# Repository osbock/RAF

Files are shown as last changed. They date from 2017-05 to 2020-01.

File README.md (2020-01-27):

# RAF - Ready...Aim...Fire!
Software for a beginning programming class with Arduino, and IOT programming with MQTT. Hardware consists of an Arduino, Shield, Pan/tilt mechanism and pneumatic components for firing foam darts
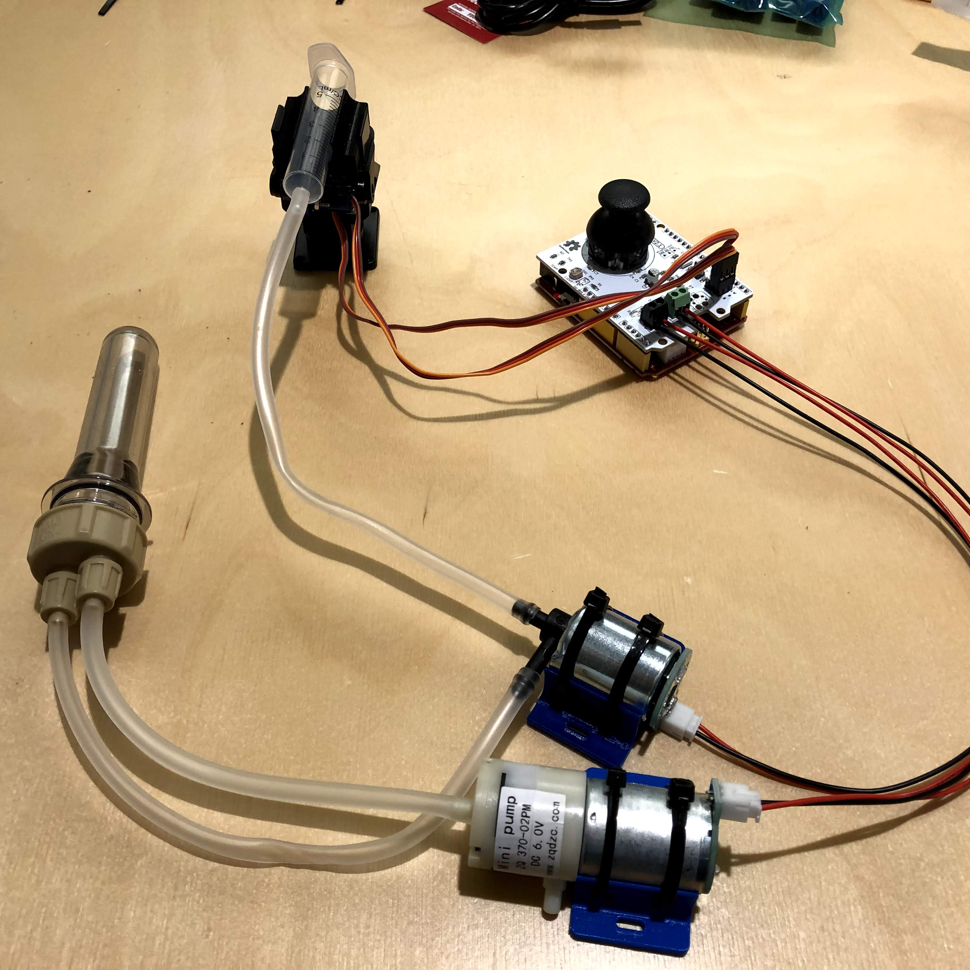
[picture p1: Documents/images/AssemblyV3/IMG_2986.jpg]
overviewpic Overview picture

## Instructions
 * [Assembly Instructions](./Documents/Assembly.md)
 * [Software setup](./Documents/Software.md)

## Software requirements
 * Arduino IDE
 * Python 3.X
 * Adafruit IOT python package

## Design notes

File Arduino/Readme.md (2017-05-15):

# Example Arduino code

 * RAFTest: basic functional test. Serial prints Light and temp sensor, joystick controls servos 3 and 5, button triggers solenoid. LED lights in sequence at boot.

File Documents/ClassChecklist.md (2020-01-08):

# Materials needed for class:
## Instructor Materials
* Assembled Demo Unit
* Extra Arduino and shield for intro to Arduino Part
* USB cable for programming (Instructor)
## Participant materials
* RAF kits (+5-7% for extra parts for failures, or extra parts)
* extra silicone tubing (ammend BOM for next order)
* zip ties (4/kit) (ammend BOM for next order) extra for hose clamp
* usb C -> usb connectors
* foam poster tape for sticking down arduino
* Power squids/extension cords
* Instruction printouts
* 8x10 foam core (1 per participant)
## tools
* 2mm flat head Screw drivers (1 per 4 participants)
* scissors
* flush cutters (optional) for cutting zip ties (can use scissors)
* wire strippers (optional for re-stripping pump and solenoid pigtails)

## Frequent failure parts
* Power Supplies
* Arduinos
* Pan tilts
* Shields
* USB cables (rare)

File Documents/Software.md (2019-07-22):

# Software Setup
 ## Arduino
  * [Arduino](https://www.arduino.cc/en/Main/Software#download)
 
   Note: download and install the desktop version. The WebIDE is untested with these course materials.
   
 ## Sample code/Arduino Libraries
 Clone or [download the zip](https://github.com/osbock/RAF/archive/master.zip) of this repository

 ## Optional setup for IOT activities
 Note: these instructions are dated and probably require updates for Python 3.x
 ## Adafruit.io
   * Get an account at [Adafruit.com](https://adafruit.com)
   * Sign up for [Adafruit.io](https://io.adafruit.com/)
   
 * [Python 2.7](https://www.python.org/downloads/release/python-2713/) (note: preinstalled on most macs)
 * Pip -- comes installed with the python.org download
 * PySerial -- pip install pyserial (sudo pip install pyserial #mac and linux)
 * [Adafruit IO](https://github.com/adafruit/io-client-python)
   * If you have pip installed, sudo pip install adafruit-io
   * otherwise, unzip repository, and python setup.py install

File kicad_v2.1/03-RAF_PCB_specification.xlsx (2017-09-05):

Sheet: Template
PCB Name 名称 | RAF Shield
Board Size 尺寸 | Length*width (Unit:mm) | 68.58 | * | 53.34
Material 板材 | (Rigid) FR－4 | Special Requirement:
Layers 层数 | 2 | Special Requirement:
Thickness 厚度 | 1.6 mm | Special Requirement:
Copper Weight 铜厚 | 1 oz. | Special Requirement:
Soldermask Color 阻焊颜色 | White | Special Requirement:
Silkscreen Color 丝印颜色 | Black | Special Requirement:
Surface Finishing 焊盘喷镀 | HASL Lead Free | Special Requirement:
Via soldermask 阻焊覆盖 | Soldermask Cover | Special Requirement:
Mini trace/spacing 最小线宽 | 0.20 mm | Special Requirement:
Mini hole size 最小孔径 | 0.40 mm | Special Requirement:
Special requirements 特殊工艺
 | Other Special requirements：

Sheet: Parameter
PCB Material | Layers | Thickness | Copper Weight | Soldermask Color | Silkscreen Color | Surface Finishing | Via soldermask | Mini trace/spacing | Mini hole size
FR-4 | 1 Layer | 0.6mm | 0.5 oz | Green | White | HASL Lead Free(RoHS) | Soldermask Cover | 4 mil or 0.10 mm | 6 mil or 0.15 mm
Flexible Printed Circuit | 2 Layer | 0.8mm | 1 oz | Red | Black | ENIG | Soldermask Opening | 5 mil or0.13 mm | 8 mil or 0.2 mm
Rogers 4003 | 4 Layer | 1.0mm | 2 oz | Blue | Yellow | OSP |  | 6 mil or 0.15 mm | 10 mil or 0.25 mm
Rogers 4350 | 6 Layer | 1.2mm | 3 oz | Black | Red | Immersion Tin |  | 8 mil or 0.20 mm | 12 mil or 0.30 mm
Taconic Series | 8 Layer | 1.3mm | Other | White | Other | Immersion Sliver
Aluminum-based material | 10 Layer | 1.6mm |  | Green Matte |  | Hard Gold
RF-35 | 12 Layer | 2.0mm |  | Blue Matte |  | Other
Arlon | 14 Layer | 2.5mm |  | Black Matte
Other | 16 Layer | 3.0mm |  | Other
 | Other | Other

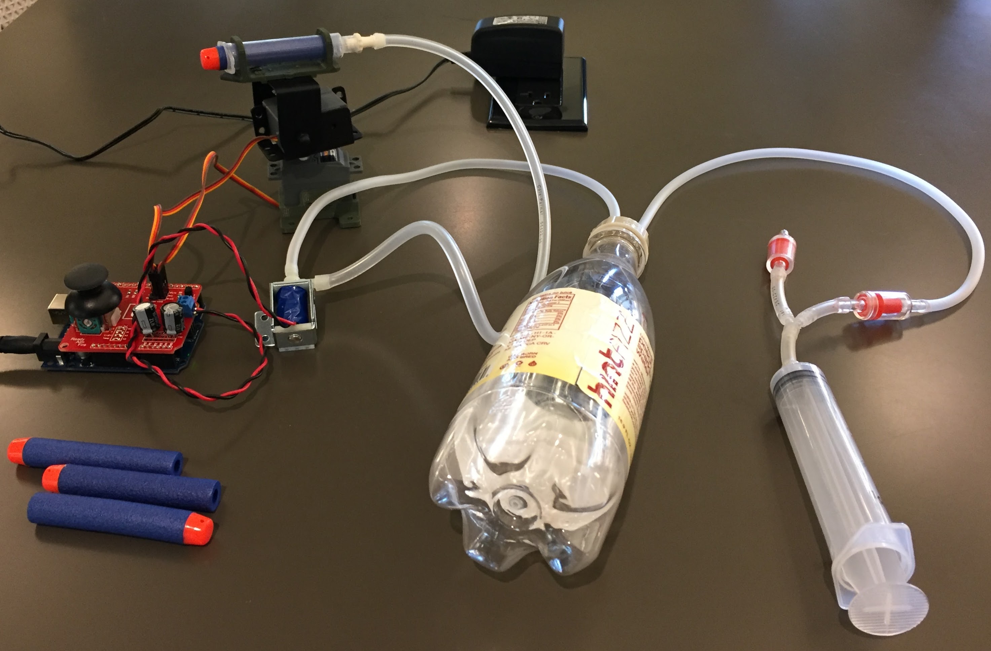
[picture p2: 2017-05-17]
Documents/images/overview.jpg

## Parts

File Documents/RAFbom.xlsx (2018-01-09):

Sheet: RAFbom
Qty | Per student BOM | Supplier link
1 | Arduino Uno R3 (make sure it has a 16u2) | http://www.microcenter.com/product/486544/Uno_R3_MainBoard
1 | USB cable for Arduino
1 | RAF Shield
2 | Servos (pan tilt mechanism)
2 | Servo extenstion cables
1 | Hardware for pan tilt mechanism.
1 | 3D printed barrel holder
1 | Gas solenoid valve | https://www.aliexpress.com/item/10PCS-LOT-DC12V-Solenoid-valve-Mini-Micro-electric-Water-Gas-valve-Discouraged-Normally-closed-6-8/32796259307.html
1 | electric air pump | https://www.aliexpress.com/item/DC-6V-Mini-Air-Pump-Motor-for-Aquarium-Tank-Oxygen-Circulate/32794737297.html
2 | 3D printed Solenoid/pump holders
1 | 9V 2.5A or greater power supply
2ft | 2 ft of air tubing
1 | 2 barb bottle cap | https://www.aliexpress.com/item/2Pcs-Aquarium-Bottle-Caps-for-DIY-CO2-System-Kit-Generator-Part-Live-Plants-Diffuser-Air-Letter/32568982068.html
1 | Barrel (5 ml Syringe) | https://www.aliexpress.com/item/100PCS-New-2016-Reusable-5ML-Large-Big-Plastic-Hydroponics-Nutrient-Measuring-Syringe/32617036933.html
5 | nerf darts | https://www.amazon.com/300-Pieces-Compatible-N-Strike-Universal-Accessories/dp/B01IQAMN4G/
1 | Soda bottle for air tank
1 | one way valves | https://www.aliexpress.com/item/10x-Aquarium-One-Way-Check-Valve-Non-Return-Fish-Tank-Air-Pump-CO2-System-Red/32705403205.html
1 | 1 luer - 1/8" hose barb adapters | https://www.aliexpress.com/item/free-shipping-100pcs-lot-1-8inch-Barb-Female-Luer-Tapered-Syringe-Fitting-polyprop-Luer-Lock-Tapered/32822131398.html
1 | Bottle holder
1 | Foam core for base
4 | Paper fasteners | https://www.staples.com/staples-gold-round-head-fasteners-3-8-width-1-capacity-100-pk/product_1804207
4 | Wire ties 5” long less than 4mm wide
2 | poster foam tape squares

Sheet: workshop tools
qty | item
20 | Scissors (air tube cutting)
20 | screwdrivers (pan tilt

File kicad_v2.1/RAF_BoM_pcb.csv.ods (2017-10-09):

Id | Designator | Package | Quantity | Designation | Supplier and ref
1 | C1,C3,C4,C5,C6,C8,C9 | C_0805_HandSoldering | 7 | 0.1uF
2 | C2,C7 | CP_Elec_4x5.7 | 2 | 22uF
3 | D1,D2 | SMA_Handsoldering | 2 | S1ATR
4 | J1,J2,J4 | Pin_Header_Straight_1x03_Pitch2.54mm | 3 | SERVO
5 | J3 | TerminalBlock_Pheonix_PT-5.0mm_2pol | 1 | SOL
6 | J5 | TerminalBlock_Pheonix_PT-5.0mm_2pol | 1 | PUMP
7 | J6 | Pin_Header_Straight_1x03_Pitch2.54mm | 1 | WS2811-OUT
8 | J7 | Pin_Header_Straight_1x04_Pitch2.54mm | 1 | I2C
9 | JOY1 | SEEED-Joystick_v2 | 1 | SeeedJoystick
10 | JP1,JP2,JP3,JP4 | 0805_jumper | 4 | Jumper_NC_Small
11 | LDR1 | Resistor_LDR_5.0x3.4 | 1 | LIGHT
12 | P1 | Socket_Strip_Arduino_1x08 | 1 | Power
13 | P2 | Socket_Strip_Arduino_1x06 | 1 | Analog
14 | P3 | Socket_Strip_Arduino_1x10 | 1 | Digital
15 | P4 | Socket_Strip_Arduino_1x08 | 1 | Digital
16 | Q1 | SuperSOT-6 | 1 | FDC6305N
17 | R1 | R_0805_HandSoldering | 1 | 22K
18 | R2 | R_0805_HandSoldering | 1 | 10K
19 | R5,R6,R7 | R_0805_HandSoldering | 3 | 100k
20 | RV1 | Res_variable | 1 | 100k
21 | TH1 | R_0805_HandSoldering | 1 | TEMP
22 | U1 | LED_WS2812B-PLCC4 | 1 | RGB_WS2811B
23 | U2 | DPak | 1 | LF60CDT
24 | H1,H2,H3,H4 | NPTH_hole_3mm | 4 | NPTH_hole
25 | OSHW1 | OSHW_6mm | 1 | OSHW
26 | WYO1 | logo_wyo_butterfly_small | 1 | LOGO_WL

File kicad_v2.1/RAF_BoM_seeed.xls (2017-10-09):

Electronic Engineering BOM List
Product Name：RAF
Version：V2.1
Issue Date：05/Sep/2017
Item No. (序号) | Reference Des (上件位置) | Qty (用量) | Catalog (分类） | Part_Description (规格描述) | Part_Value （元件值） | Part_Package （元件封装） | Manufacturers Name (使用厂牌名称) | Manufacturers Part No. (使用厂牌型号) | Distributors Name （供应商名称） | Distributors Part No. (供貨商型号) | Notes/Remark （备注）
Example（填写范例）
1 | U1 | 1 | OTHER | 5050 SMD RGB LED with built-in controller | WS2812B | 5050 | - | WS2812B | Aliexpress | WS2812B (4 pin version) | http://www.aliexpress.com/item/WS2812B-4pins-5050-SMD-W-WS2811-Individually-Addressable-Digital-RGB-LED-Chip-5V/1639139960.html
2 | U2 | 1 | IC | 6V LDO regulator | LF60CDT-TR | TO-252-3 DPAK | STMicroelectronics | LF60CDT-TR | Digikey | 497-15653-1-ND (https://www.digikey.com/product-detail/en/stmicroelectronics/LF60CDT-TR/497-15653-1-ND/5253745)
3 | Q1 | 1 | Transistor | dual Mosfet | FDC6305N | SuperSOT-6 | Fairchild/ON Semiconductor | FDC6305N | Digikey | FDC6305NCT-ND (https://www.digikey.com/product-detail/en/fairchild-on-semiconductor/FDC6305N/FDC6305NCT-ND/965582)
4 | P1, P4 | 2 | Connector | Header, Male, 8x1 | -- | Through hole, 0.100" (2.54mm) | Amphenol FCI | 68001-108HLF | Digikey | 609-3273-ND (https://www.digikey.com/product-detail/en/amphenol-fci/68001-108HLF/609-3273-ND/1878534) | Generic ok
5 | P2 | 1 | Connector | Header, Male, 6x1 | -- | Through hole, 0.100" (2.54mm) | Amphenol FCI | 68001-106HLF | Digikey | 609-3272-ND (https://www.digikey.com/product-detail/en/amphenol-fci/68001-106HLF/609-3272-ND/1878473) | Generic ok
6 | P3 | 1 | Connector | Header, Male, 10x1 | -- | Through hole, 0.100" (2.54mm) | Amphenol FCI | 68001-110HLF | Digikey | 609-3274-ND (https://www.digikey.com/product-detail/en/amphenol-fci/68001-110HLF/609-3274-ND/1878506) | Generic ok
7 | J1,J2,J4 | 3 | Connector | Pin_Header_Straight_1x03_Pitch2.54mm | SERVO | Through hole, 0.100" (2.54mm) | Amphenol FCI | 68001-203HLF | Digikey | 609-3470-ND (https://www.digikey.com/product-detail/en/amphenol-fci/68001-203HLF/609-3470-ND/2023312) | Generic ok
8 | R1 | 1 | Resister | RES SMD 22K OHM 1% 1/8W 0805 | 22k | 0805 | Yageo | RC0805FR-0722KL | Digikey | 311-22.0KCRCT-ND (https://www.digikey.com/product-detail/en/yageo/RC0805FR-0722KL/311-22.0KCRCT-ND/730683) | Generic ok
9 | R2 | 1 | Resister | RES 10K OHM 1/8w 1% 0805 | 10k | 0805 | Yageo | RC0805FR-0710KL | Digikey | 311-10.0KCRCT-ND (https://www.digikey.com/product-detail/en/yageo/RC0805FR-0710KL/311-10.0KCRCT-ND/730482) | Generic ok
10 | R5,R6,R7 | 3 | Resister | RES 100K OHM 1/8w 1% 0805 | 100k | 0805 | Yageo | RC0805FR-07100KL | Digikey | 311-100KCRCT-ND (https://www.digikey.com/product-detail/en/yageo/RC0805FR-07100KL/311-100KCRCT-ND/730491) | Generic ok
11 | C1,C3,C4,C5,C6,C8,C9 | 7 | Capacitor | CAP CER 0.1UF 50V X7R 0805 | 0.1uF | 0805 | AVX Corporation | 08055C104MAT2A | Digikey | 478-3351-1-ND (https://www.digikey.com/product-detail/en/avx-corporation/08055C104MAT2A/478-3351-1-ND/930143) | Generic ok
12 | C2,C7 | 2 | Capacitor | Electrolytic Cap 22 uF | 22uF | Radial, Can - SMD | Panasonic | EEE-1CA220WR | Digikey | PCE3882CT-ND (https://www.digikey.com/product-detail/en/panasonic-electronic-components/EEE-1CA220WR/PCE3882CT-ND/766258) | Generic ok
13 | JOY1 | 1 | OTHER | SEEED Thumb joystick |  |  | SEEED | SKU 311110005 | SEEED | SKU 311110005 (https://www.seeedstudio.com/Analog-joystick-p-282.html)
14 | J3 | 1 | Connector | 2 Pos screw terminal 5mm pitch | -- |  | Phoenix Contact | 1985849 | Digikey | 277-9145-ND (https://www.digikey.com/scripts/DkSearch/dksus.dll?Detail&itemSeq=238724152) | It would be nice if
15 | J5 | 1 | Connector | 2 Pos screw terminal 5mm pitch | -- |  | Phoenix Contact | 1729018 | Digikey | 277-1236-ND (https://www.digikey.com/scripts/DkSearch/dksus.dll?Detail&itemSeq=238724168&uq=636413384256513315) | These were different colors
16 | LDR1 | 1 | OTHER | PHOTOCELL 16-33KOHM | 22k | Through hole, 0.100" (2.54mm) | Luna Optoelectronics | PDV-P8103 | Digikey | PDV-P8103-ND (https://www.digikey.com/product-detail/en/PDV-P8103/PDV-P8103-ND/480610)
17 | S1 | 1 | OTHER | 6mm tactile switch smd | MISO | SMD | C&K | PTS645SM43SMTR92 LFS | Digikey | CKN9112CT-ND (https://www.digikey.com/product-detail/en/c-k/PTS645SM43SMTR92-LFS/CKN9112CT-ND/1146934)
18 | TH1 | 1 | Resister | 0805 NTC Thermistor 10k 5% | 10k | 0805 | Murata | NCP21XV103J03RA | Digikey | 490-2456-1-ND (https://www.digikey.com/product-detail/en/murata-electronics-north-america/NCP21XV103J03RA/490-2456-1-ND/588670)
Do Not Populate
19 | J6 | 1 | Connector | Pin_Header_Straight_1x03_Pitch2.54mm | WS2811_OUT | Through hole, 0.100" (2.54mm) | Amphenol FCI | 68001-203HLF | Digikey | 609-3470-ND (https://www.digikey.com/product-detail/en/amphenol-fci/68001-203HLF/609-3470-ND/2023312) | Generic ok
20 | J7 | 1 | Connector | Pin_Header_Straight_1x04_Pitch2.54mm | I2C | Through hole, 0.100" (2.54mm) | Amphenol FCI | 68000-204HLF | Digikey | 609-3255-ND (https://www.digikey.com/product-detail/en/amphenol-fci/68000-204HLF/609-3255-ND/1878484) | Generic ok
21 | JP1,JP2,JP3,JP4 | 4 | Resister | Res 0 OHM 1/8W 0805 | 0 | 0805 | Yageo | RC0805JR-070RL | Digikey | 311-0.0ARCT-ND (https://www.digikey.com/product-detail/en/yageo/RC0805JR-070RL/311-0.0ARCT-ND/731163) | Generic ok
22 | D1,D2 | 2 | Diode | DIODE GEN PURP 50V 1A SMA | S1ATR | SMA | SMC Diode Solutions | S1ATR | Digikey | 1655-1502-1-ND (https://www.digikey.com/product-detail/en/smc-diode-solutions/S1ATR/1655-1502-1-ND/6022947)
23 | RV1 | 1 | OTHER | 0.1W, 1/10W J Lead Surface Mount Trimmer Potentiometer Cermet 1 Turn Top Adjustment | 100k | Surface Mount, J Lead, Rectangular - 0.150" x 0.142" Face x 0.047" H (3.80mm x 3.60mm x 1.20mm) | Bourns Inc. | TC33X-2-104E | Digikey | TC33X-104ECT-ND (https://www.digikey.com/product-detail/en/bourns-inc/TC33X-2-104E/TC33X-104ECT-ND/612912) | Generic ok
1. Recommended Distributor: Digi-Key, Mouser, Avnet Express, Farnell.
2. Catalog: Capacitor,Resister,Diode,Connector,Transistor,IC,PROTECTOR CATEGORY,OTHER
3. Required Fields: Item No, Reference Des, Qty, Catalog, Part_Value, Part Package
Optional Fields: Part_Description, Manufacturers Name, Manufacturers Part No, Distributors Name, Distributors Part No, Unit Cost, Price break to use, Notes/Remark

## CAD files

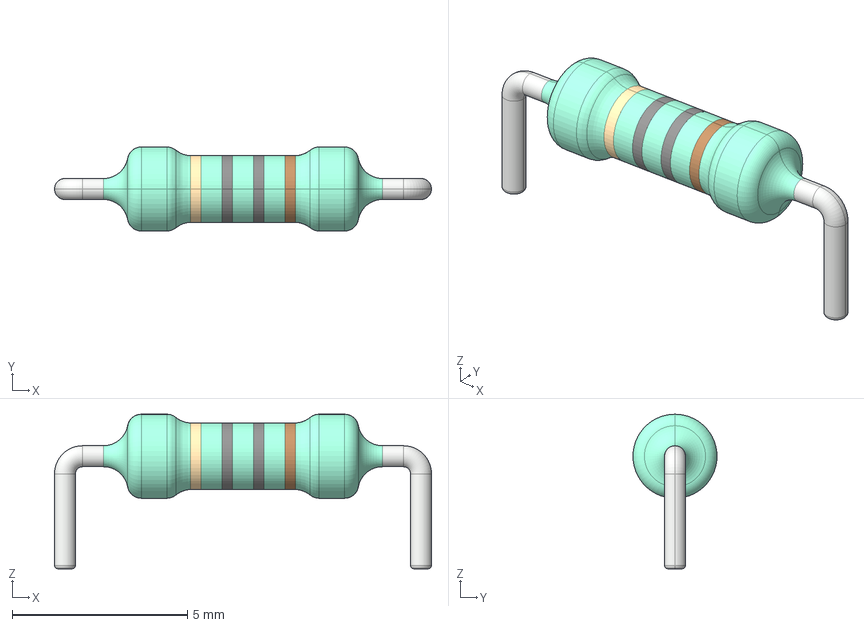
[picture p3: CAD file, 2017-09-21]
aux_test_pcb/aux_test_3D/Res40-Axial_Short_0.25W-10R.step
10.8 x 2.40 x 4.41 mm

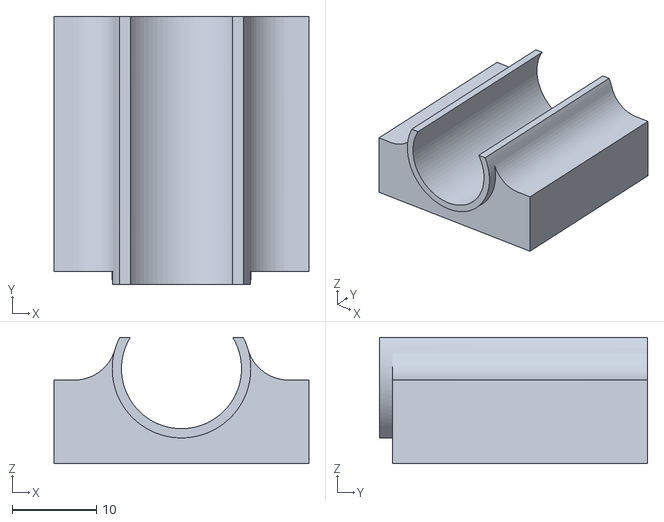
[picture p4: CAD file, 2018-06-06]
fabricate/BarrelHolder.stl
30.2 x 31.8 x 15.0

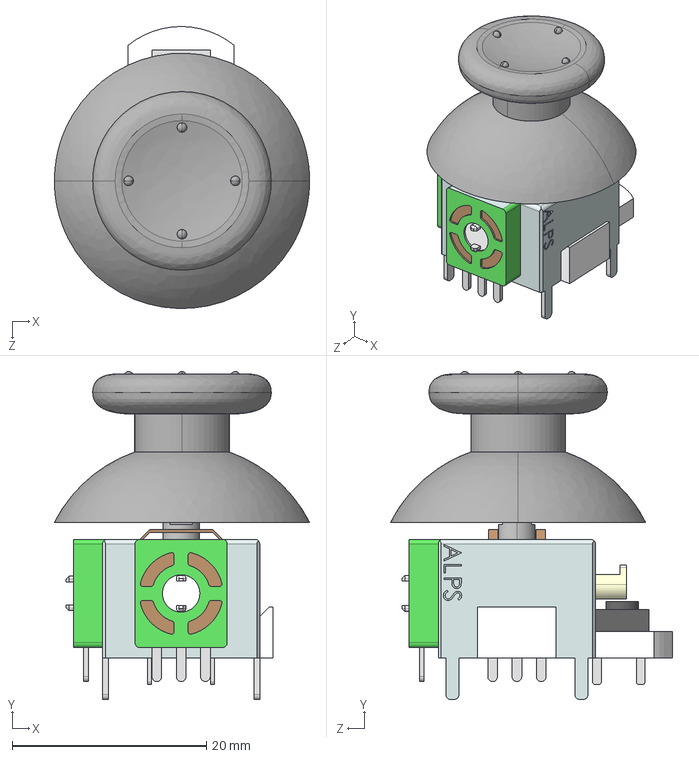
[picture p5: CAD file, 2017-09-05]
kicad_v2.1/RAF_3D/ALPS_JOYSTICK.step
26.3 x 33.8 x 29.0 mm
User Library-ALPS JOYSTICK_User Library-Joystick_Asm_Left_Joystick_b
User Library-ALPS JOYSTICK_User Library-alps joystick module

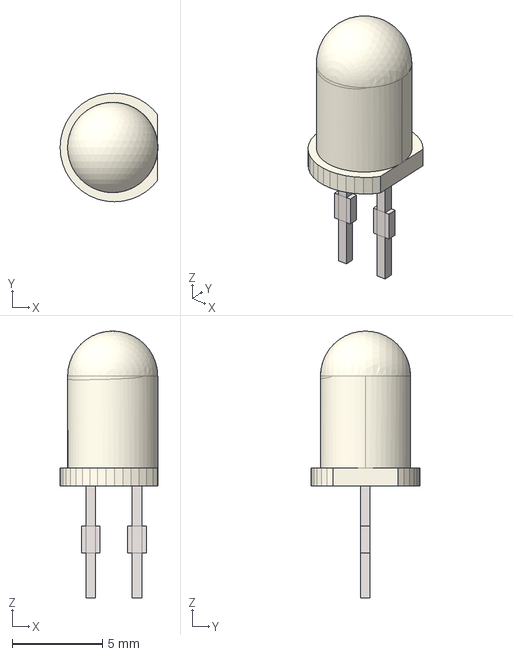
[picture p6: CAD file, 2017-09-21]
aux_test_pcb/aux_test_3D/LED_5mm.step
5.42 x 6.02 x 14.8 mm

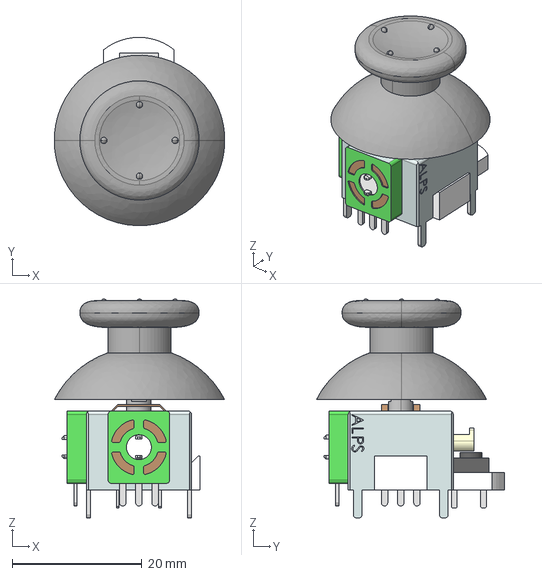
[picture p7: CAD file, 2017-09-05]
kicad_v2.1/RAF_3D/seeed_joystick_2.step
26.3 x 29.0 x 33.8 mm

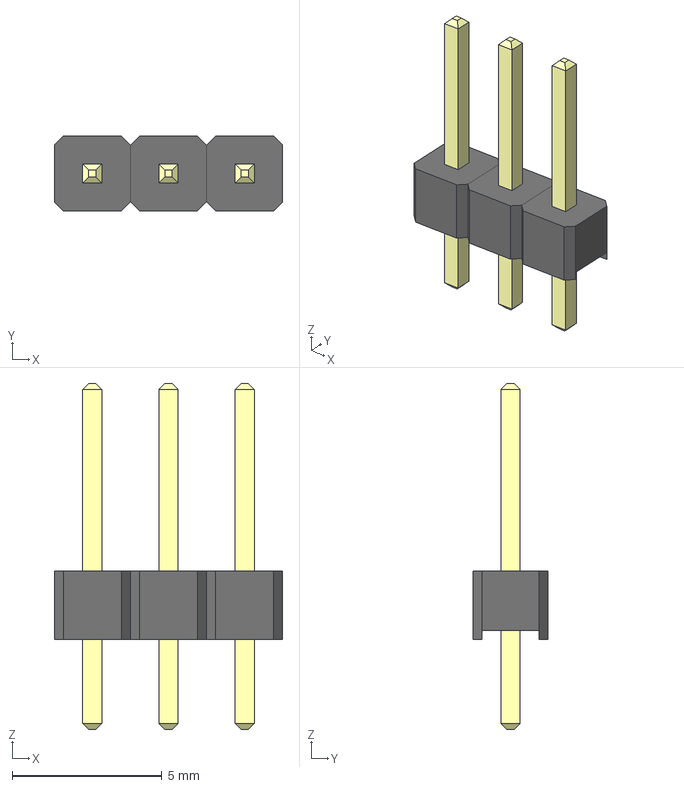
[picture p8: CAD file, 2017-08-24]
aux_test_pcb/aux_test_3D/Header_Male_03Pin.step
7.62 x 2.49 x 11.5 mm

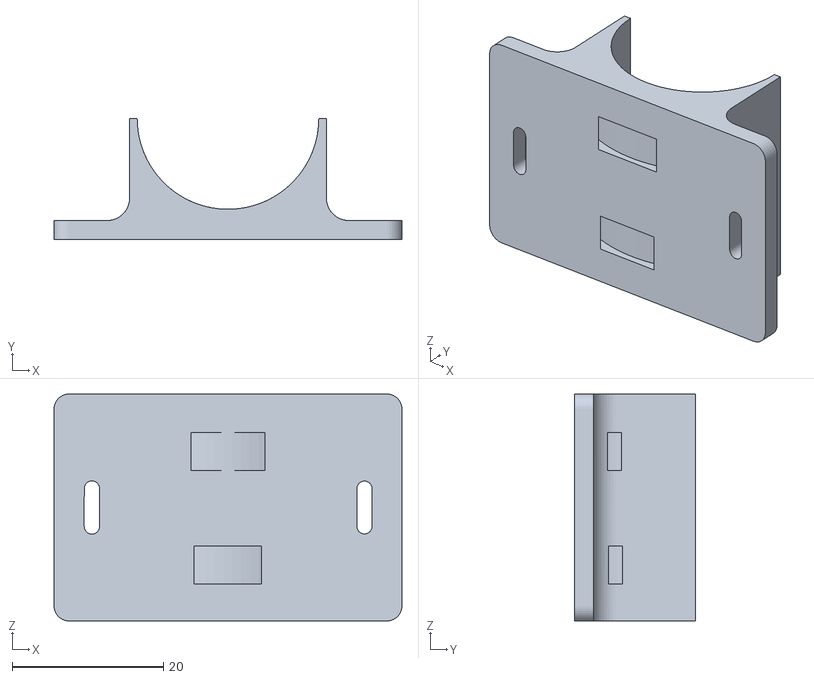
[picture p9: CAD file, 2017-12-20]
fabricate/solenoid_holder.stl
46.0 x 16.0 x 30.0

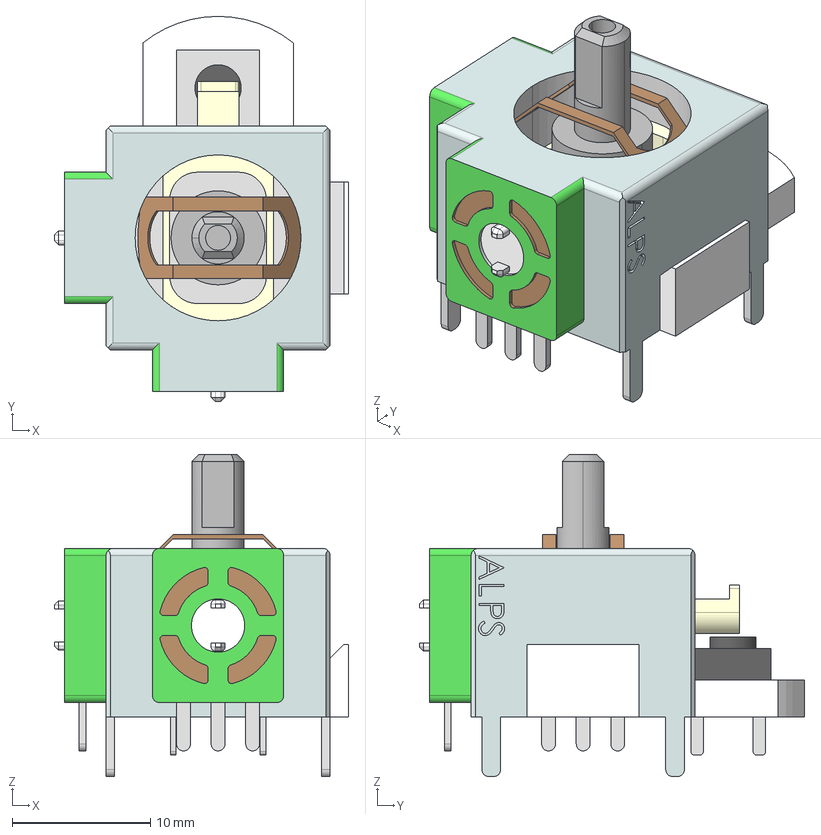
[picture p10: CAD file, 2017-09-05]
kicad_v2.1/RAF_3D/seeed_joystick.step
21.3 x 27.9 x 23.3 mm

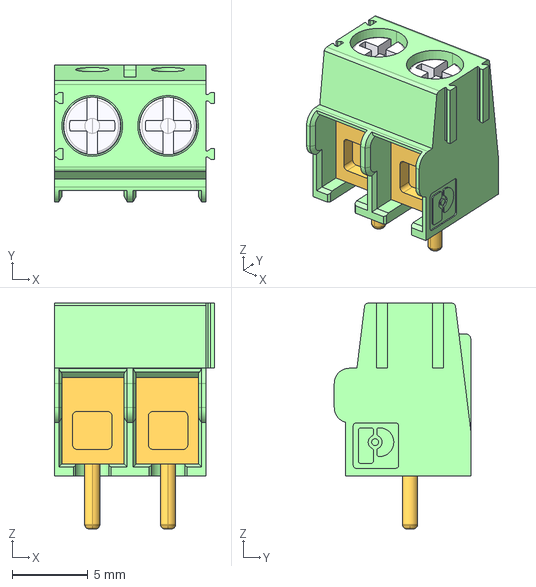
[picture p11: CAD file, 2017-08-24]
aux_test_pcb/aux_test_3D/TerminalBlock_Pheonix_PT-5.0mm_2pol.step
10.6 x 9.00 x 14.9 mm

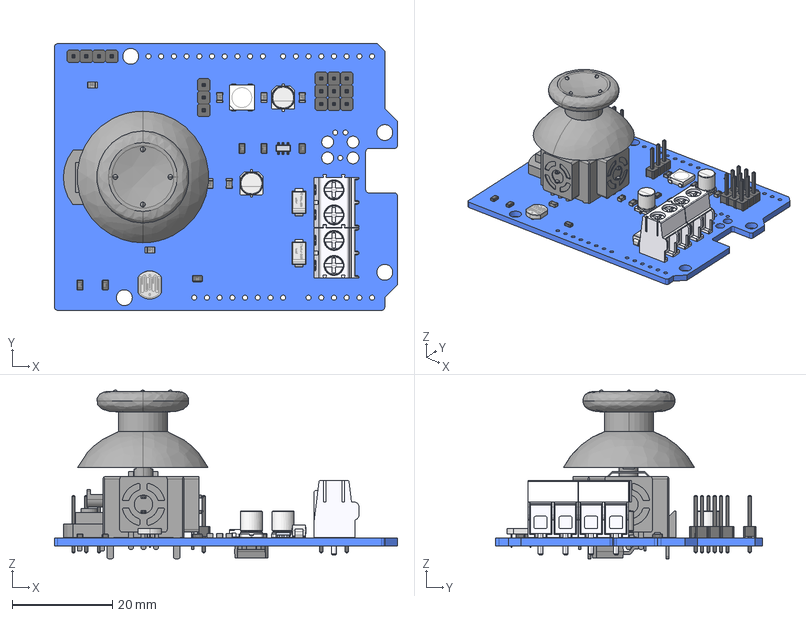
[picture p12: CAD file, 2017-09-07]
fabricate/RAF.FCStd
68.6 x 53.3 x 33.8 mm
Pcb
Header_Male_03Pin_
CP_Elec_4x5_7_
LED_WS2812_
SW3dPS-0805_SMD_Resistor_
SW3dPS-0805_SMD_Resistor_001
SW3dPS-0805_SMD_Resistor_002
SW3dPS-0805_SMD_Resistor_003
SW3dPS-0805_SMD_Resistor_004
SW3dPS-0805_SMD_Resistor_005
SuperSOT23_
Header_Male_04Pin_
Header_Male_03Pin_001
Header_Male_03Pin_002
Header_Male_03Pin_003
User_Library-DIOM5528X26_
User_Library-DIOM5528X26_001
User_Library-CapCeramic_Kemet_0805_2012_
User_Library-CapCeramic_Kemet_0805_2012_001
User_Library-CapCeramic_Kemet_0805_2012_002
User_Library-CapCeramic_Kemet_0805_2012_003
User_Library-CapCeramic_Kemet_0805_2012_004
User_Library-CapCeramic_Kemet_0805_2012_005
User_Library-CapCeramic_Kemet_0805_2012_006
CP_Elec_4x5_7_001
User_Library-DPAK_TO-252AA_
Scale_
TerminalBlock_Pheonix_PT-5.0mm_2pol_
TerminalBlock_Pheonix_PT-5.0mm_2pol_001
seeed_joystick_2_

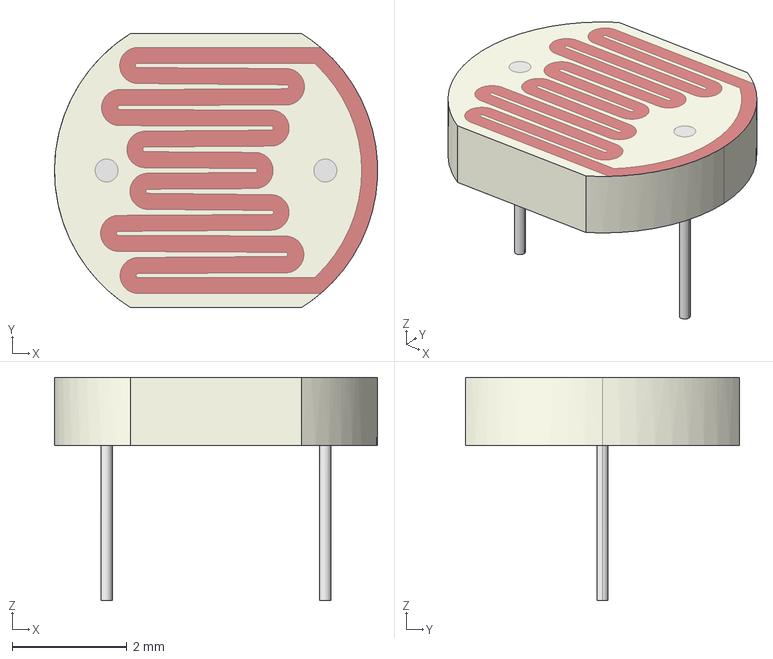
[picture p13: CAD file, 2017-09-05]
kicad_v2.1/RAF_3D/Resistor_LDR_5_0x3_4.step
5.62 x 4.77 x 3.89 mm

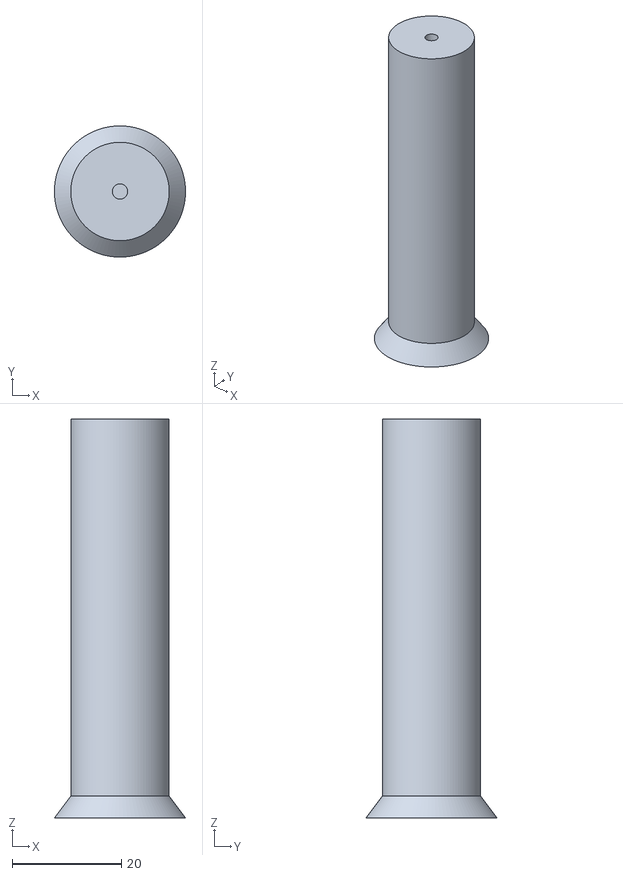
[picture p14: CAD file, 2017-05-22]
fabricate/leg.stl
24.0 x 24.0 x 73.0

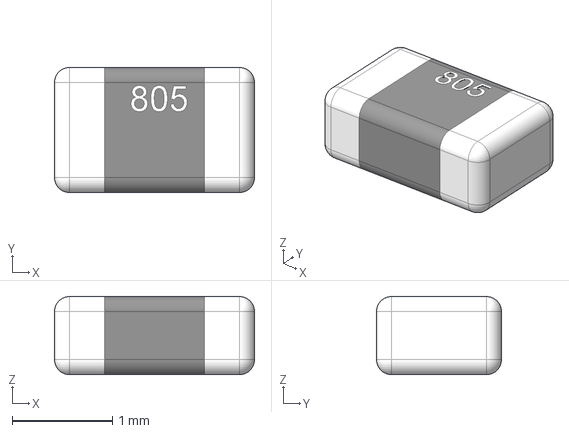
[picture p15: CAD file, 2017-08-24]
kicad_v2.1/RAF_3D/r_0805.step
2.00 x 1.25 x 0.782 mm

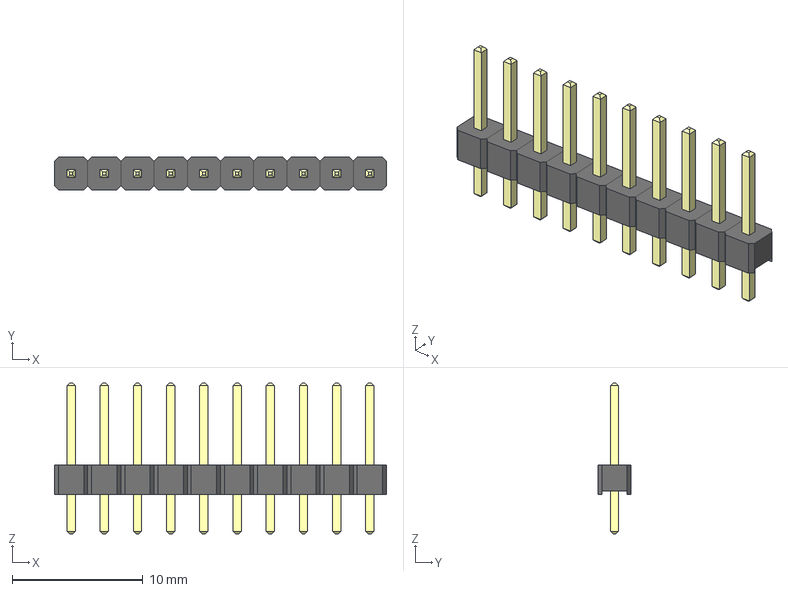
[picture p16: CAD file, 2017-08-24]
kicad_v2.1/RAF_3D/Header_Male_10Pin.step
25.4 x 2.49 x 11.5 mm

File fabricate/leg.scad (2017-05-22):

$fn=99;
difference (){
    union(){
        cylinder(h = 73, d = 18);
        cylinder(h=4,r1=12,r2=9);
    }

        translate([0,0,63])cylinder(h = 12, d = 2.8);
        translate([0,0,-1])cylinder(h = 12, d = 2.8);
}

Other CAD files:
kicad_v2.1/RAF_3D/Header_Male_04Pin.step
kicad_v2.1/RAF_3D/DO-214AC_SMA.step
kicad_v2.1/RAF_3D/Header_Male_08Pin.step
kicad_v2.1/RAF_3D/c_0805.step
fabricate/BarrelHolder v9.stl
kicad_v2.1/RAF_3D/CP_Elec_4x5_7.step
kicad_v2.1/RAF_3D/DPAK_TO-252AA.step
kicad_v2.1/RAF_3D/Header_Male_06Pin.step
kicad_v2.1/RAF_3D/LED_WS2812.step
kicad_v2.1/RAF_3D/Resistor-0805_SMD.step
kicad_v2.1/RAF_3D/Resistor_LDR_4_9x4_2_RM2_54.step
kicad_v2.1/RAF_3D/SOT23-6-4.step
kicad_v2.1/RAF_3D/SOT23-6.step
kicad_v2.1/RAF_3D/SW_smd.step
kicad_v2.1/RAF_3D/SuperSOT23.step

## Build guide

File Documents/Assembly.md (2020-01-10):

# Hardware Assembly
This is what the fully assembled kit will look like when we are finished

Final Assembly

## Unpack your kit
Layout the contents on a table, putting like things together

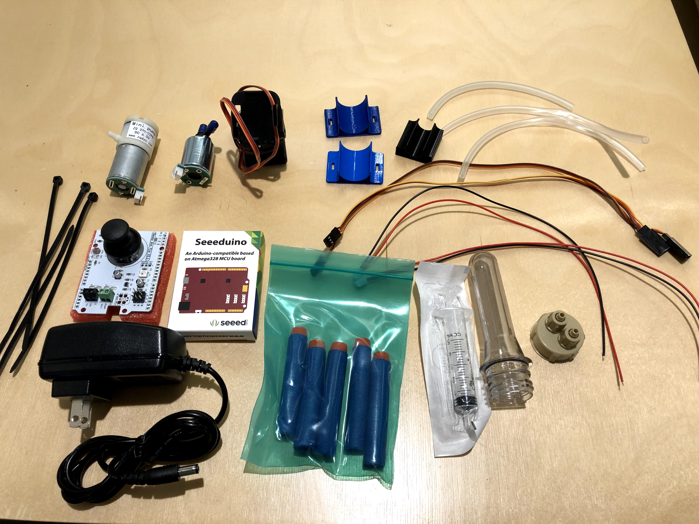
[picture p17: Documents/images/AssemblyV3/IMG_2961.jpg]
Knolled parts


## Solenoid and pump preparation. Preparation

First perpare your gas solenoid (electronically controlled air release valve).
Take off the blue caps from the inputs/outputs of the valve
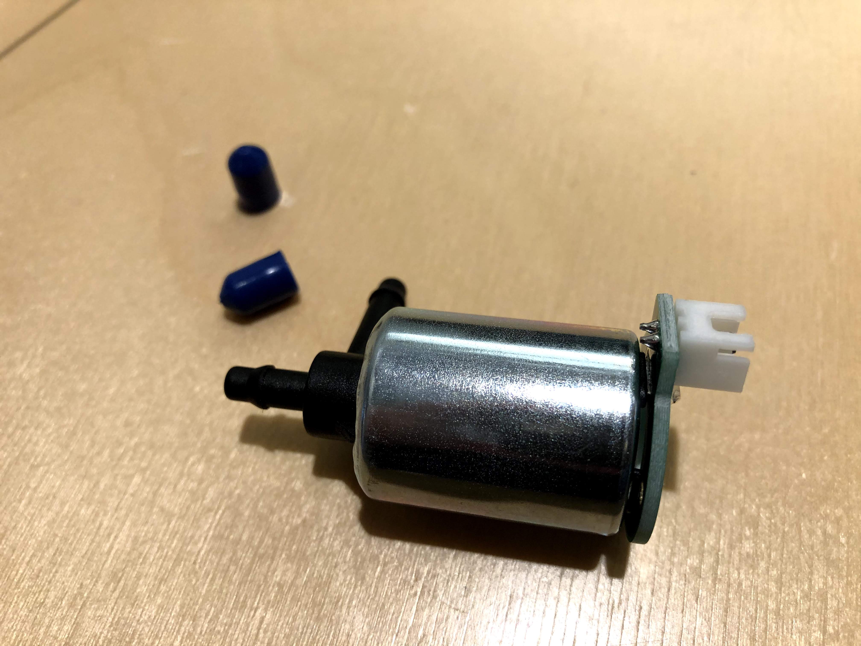
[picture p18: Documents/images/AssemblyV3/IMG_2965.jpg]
Caps Off


There are two sets of leads with a white JST connector on one end connect one to the matching connector on the board on the back of the solenoid.

Feed the Zip ties through the channels in the bottom of one of the 3D printed holders. Note the orientation of the zip tie. Do this for both channels (x2)
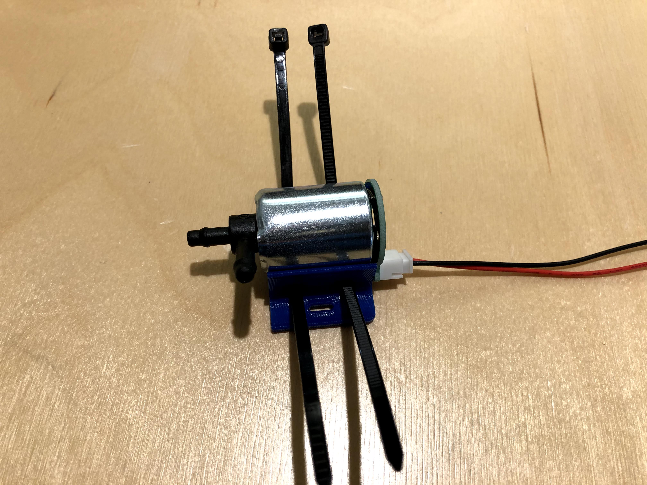
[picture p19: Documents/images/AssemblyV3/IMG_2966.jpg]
leads on


Place the Solenoid valve in the cradle, and fasten the zip ties around it, tighten and clip off the excess.
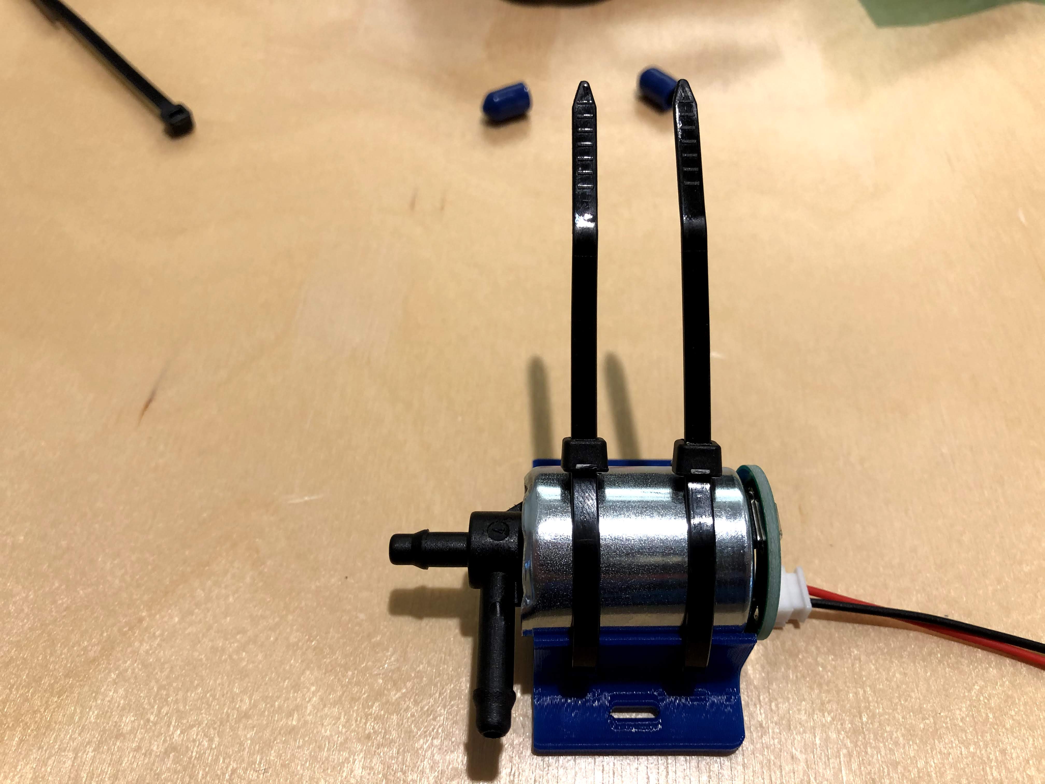
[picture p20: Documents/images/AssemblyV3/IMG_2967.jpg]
zipit good


Prepare the other cradle the same way and fasten the pump to it.
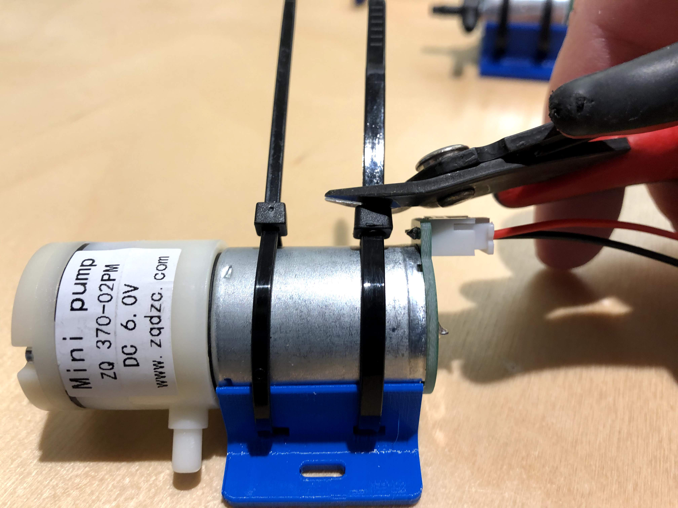
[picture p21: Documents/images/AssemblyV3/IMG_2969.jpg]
zip pump


## Barrel assembly
Remove the plunger from the 5ml Syringe. Discard (unless you can think of a cool use...)
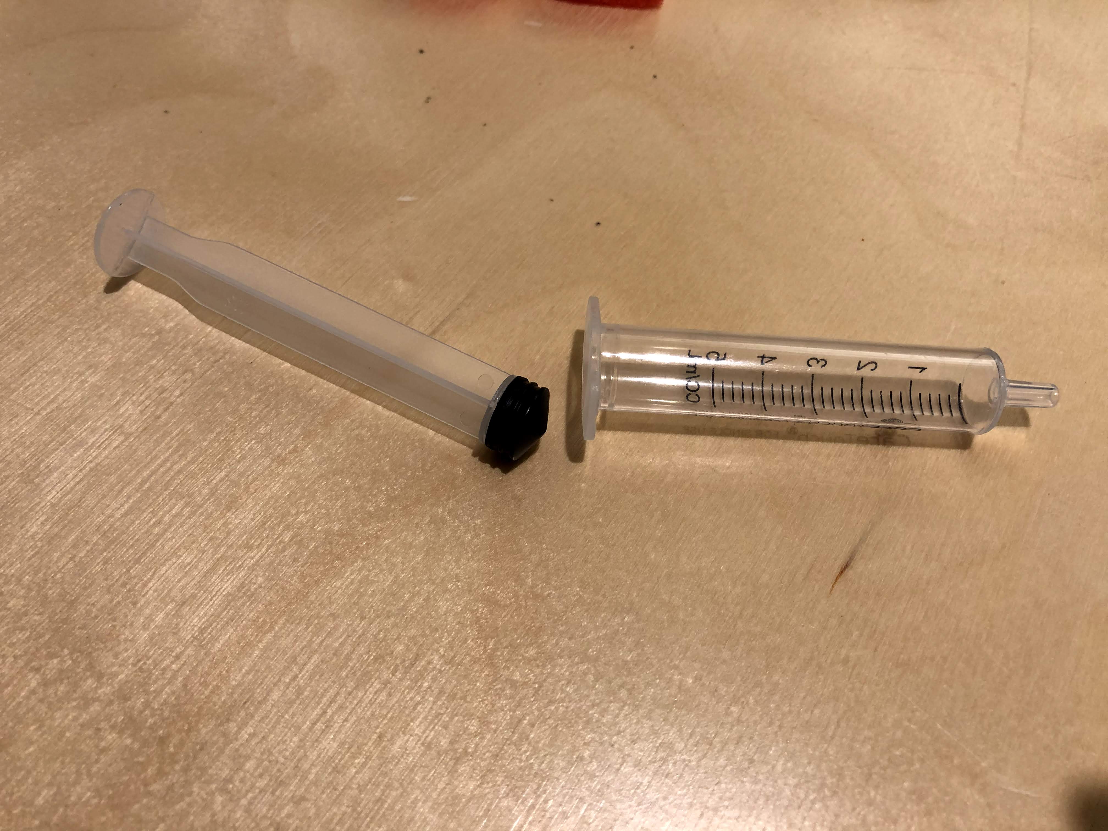
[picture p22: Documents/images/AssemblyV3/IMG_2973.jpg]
plunger removal


Slip the syringe into the barrel holder 3D printed part and snap into the Pan-tilt mechanism. Note that the "handle end" of the syringe (front of the barrel) points away from where the leads come out of the pan-tilt.
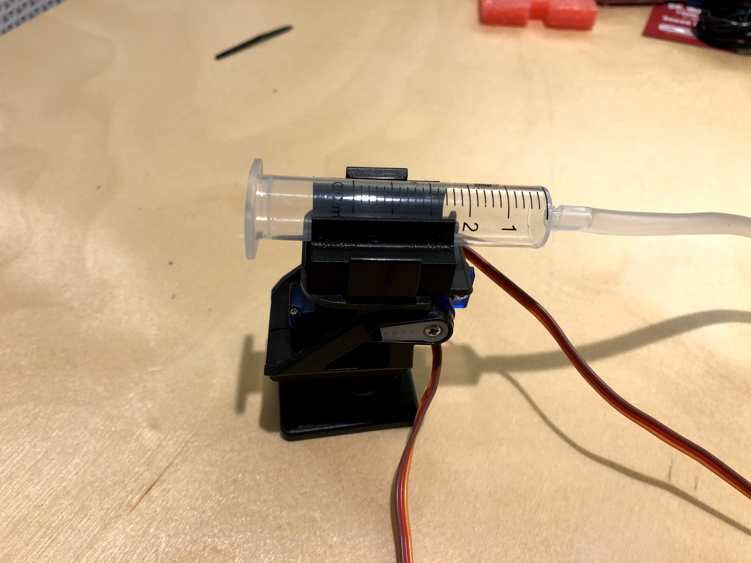
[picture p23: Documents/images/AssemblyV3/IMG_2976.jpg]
Barrel assembly


Cut approximately 5-6" of tubing and connect between the barb on the syringe and the front (axial) valve of the solenoid valve. If you dont have the Luer-barb, or have a syringe with a slip on style end, just slide the tubing over that.
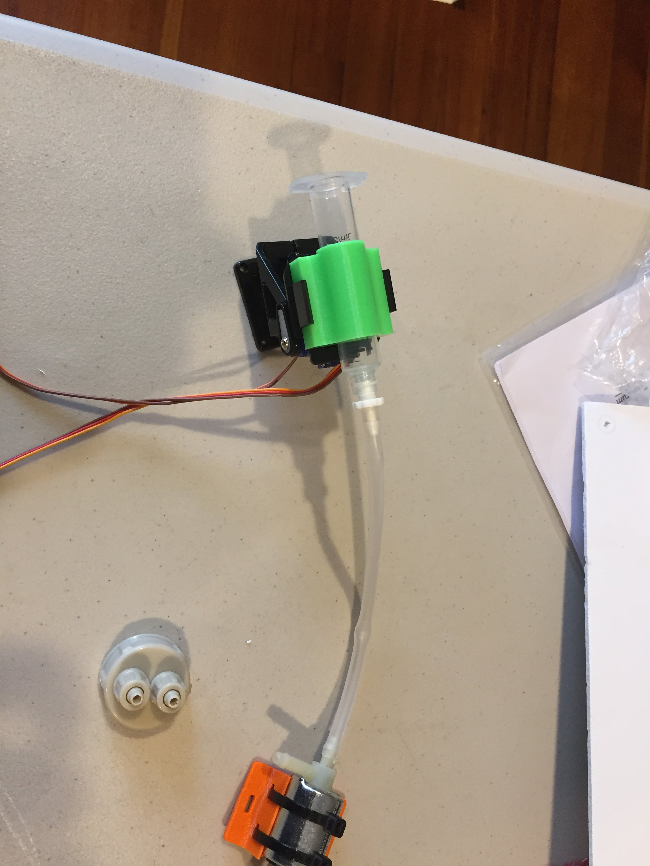
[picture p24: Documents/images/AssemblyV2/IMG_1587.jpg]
first tubing


## Pressure Vessel
Unscrew the two caps from the "two barb" bottle cap. These slip over the tubing, the tubing over the barb and then screw the caps down over the tubing.
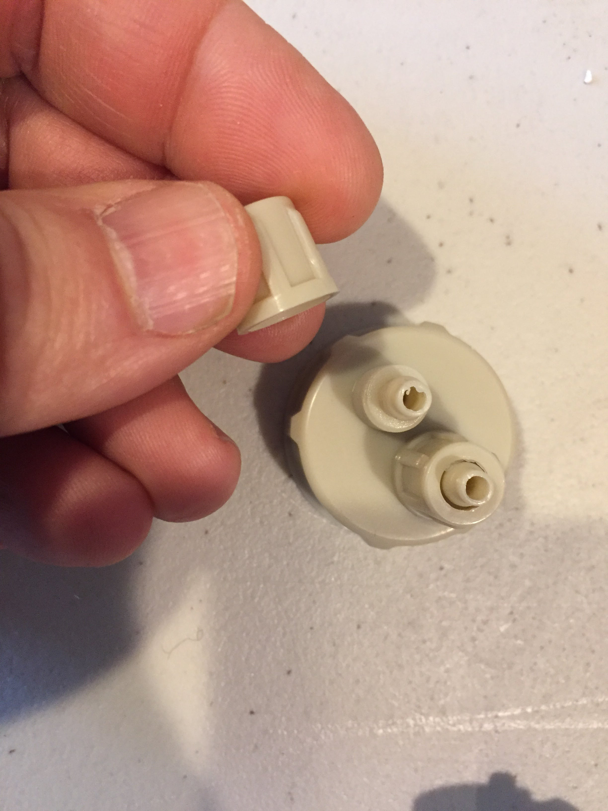
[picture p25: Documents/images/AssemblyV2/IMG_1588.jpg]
cap prep

Attach approximately 8" of tubing to the other barb of the solenoid valve, slide the retaining cap over the other end, and fasten to the bottle cap barb.
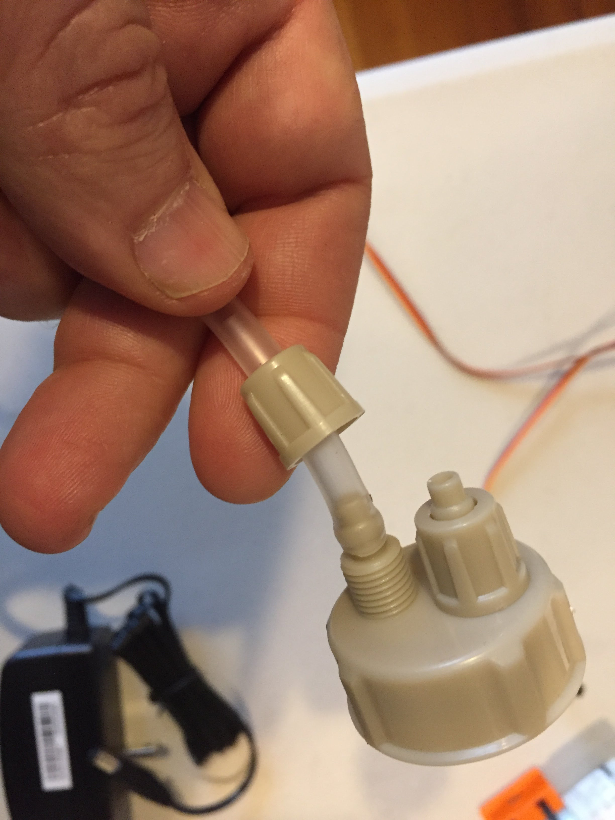
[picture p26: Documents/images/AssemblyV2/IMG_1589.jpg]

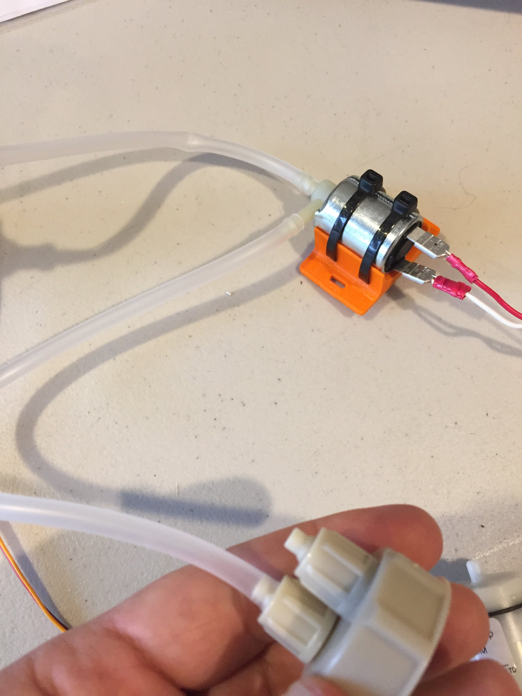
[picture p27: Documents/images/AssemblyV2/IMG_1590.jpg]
solenoid attach


Take another 8" piece and cut it in two pieces (one can be shorter, it doesn't matter) we'll be putting a 1-way valve inline here and connecting the pump to the pressure vessel
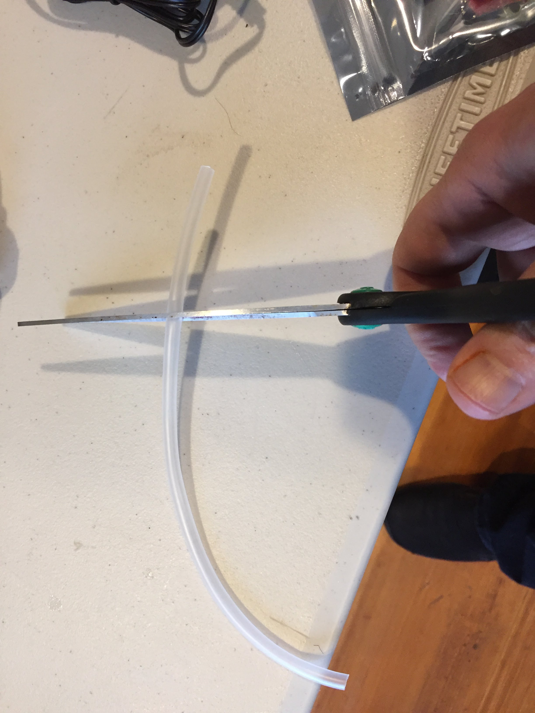
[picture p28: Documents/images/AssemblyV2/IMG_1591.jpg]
tubing cut


Slide the tubing over the ends of the oneway valve. The disk part (shown here with a short tube attached) goes toward the pump.
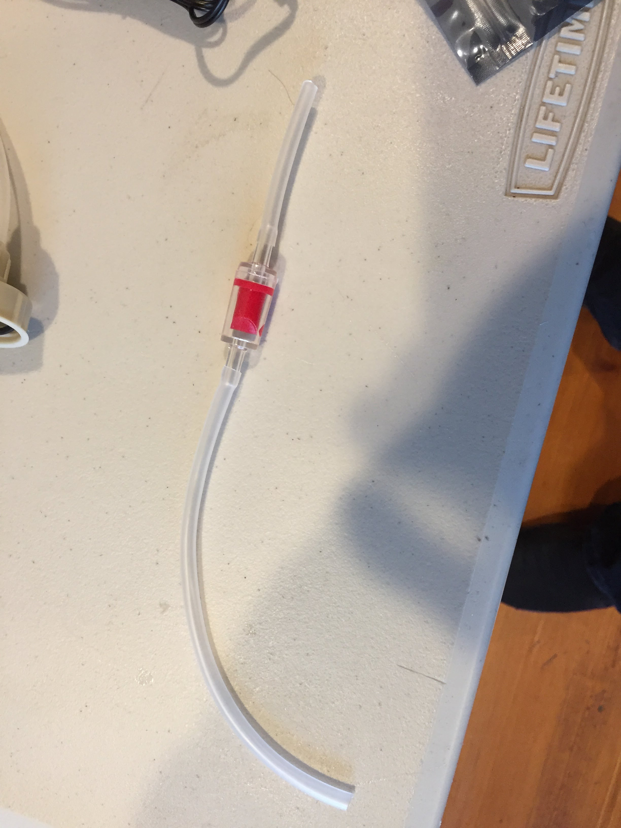
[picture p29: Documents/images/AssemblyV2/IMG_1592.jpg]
valve attach


Attach the other end (away from the disk) to the pressure cap
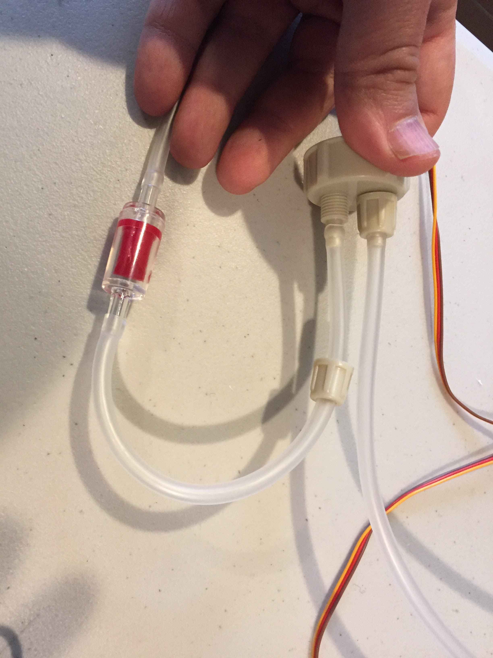
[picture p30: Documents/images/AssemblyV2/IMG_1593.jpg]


Finally Attach the remaining end to the pump output. If your pump has two barbs it's the one on the end (not the side) axially aligned with the length of the pump.
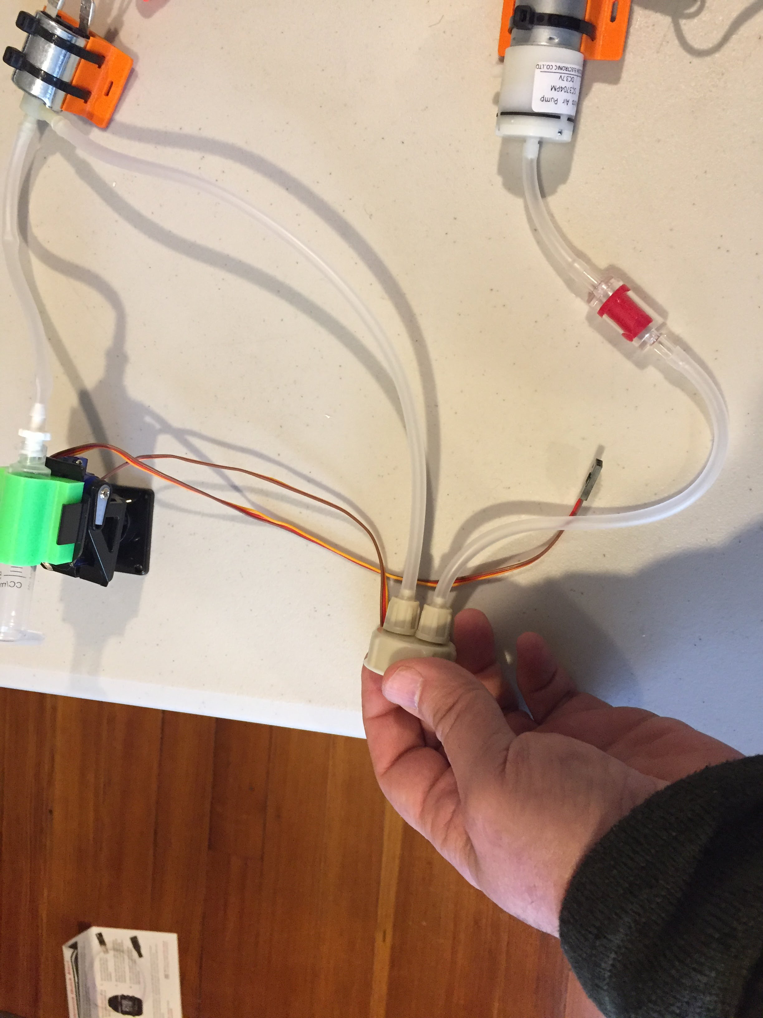
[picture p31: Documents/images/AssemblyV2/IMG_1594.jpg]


Next screw on your pressure vessel (soda bottle) this completes the Pneumatic assembly. This picture also gives you a good view of all the connections. make sure yours looks like this.
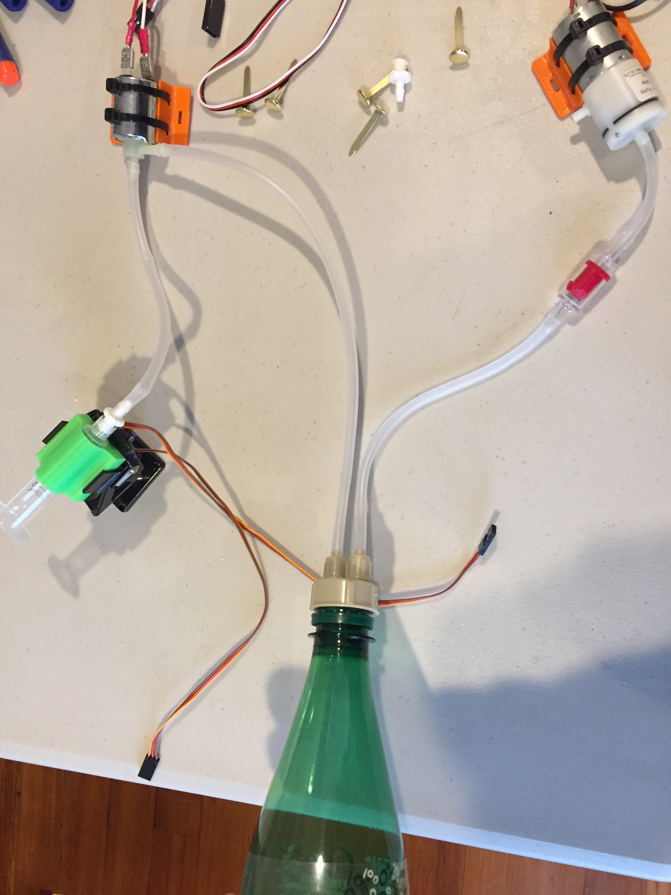
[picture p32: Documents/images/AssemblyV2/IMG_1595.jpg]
bottle


## Electronics assembly
Take the RAF shield from the antistatic bag (it's the board with a joystick). Also remove the Arduino from it's packaging, and line up the pins from shield to the Arduino. Note that there are more pins on one side than the other, make sure you have the right headers on both sides. Carefully press them together straight down.
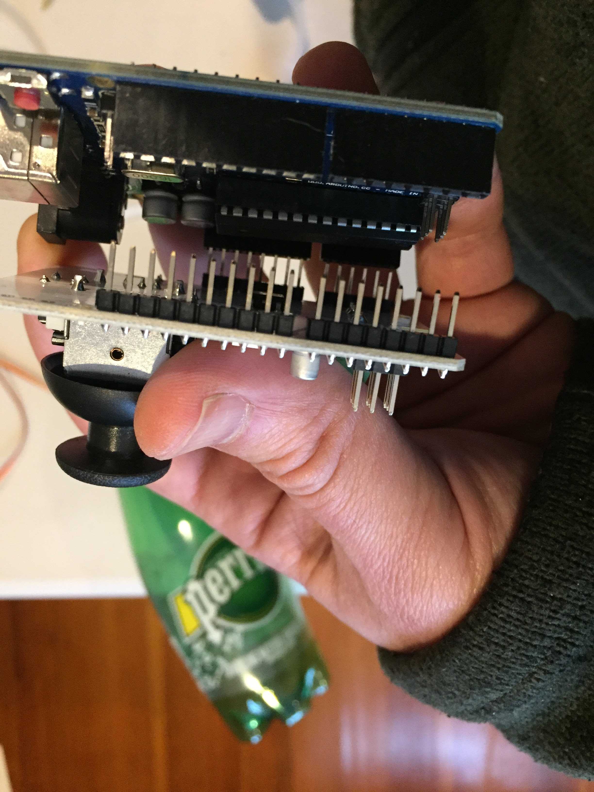
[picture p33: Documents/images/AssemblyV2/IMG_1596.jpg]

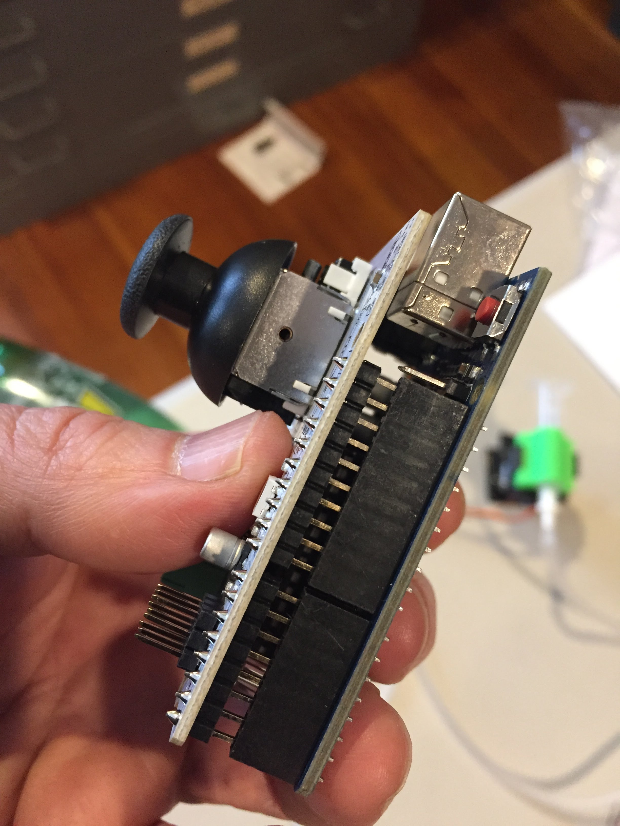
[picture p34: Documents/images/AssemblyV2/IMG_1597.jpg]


Attach the leads from the pump to the screw terminals (inside set, near the middle of the end of the shield) labeled PUMP. Make sure the screws are screwed out first to reveal a little hole to stick the wires in. Stick a wire in and tighten by screwing clockwise. Note that polarity doesn't matter.
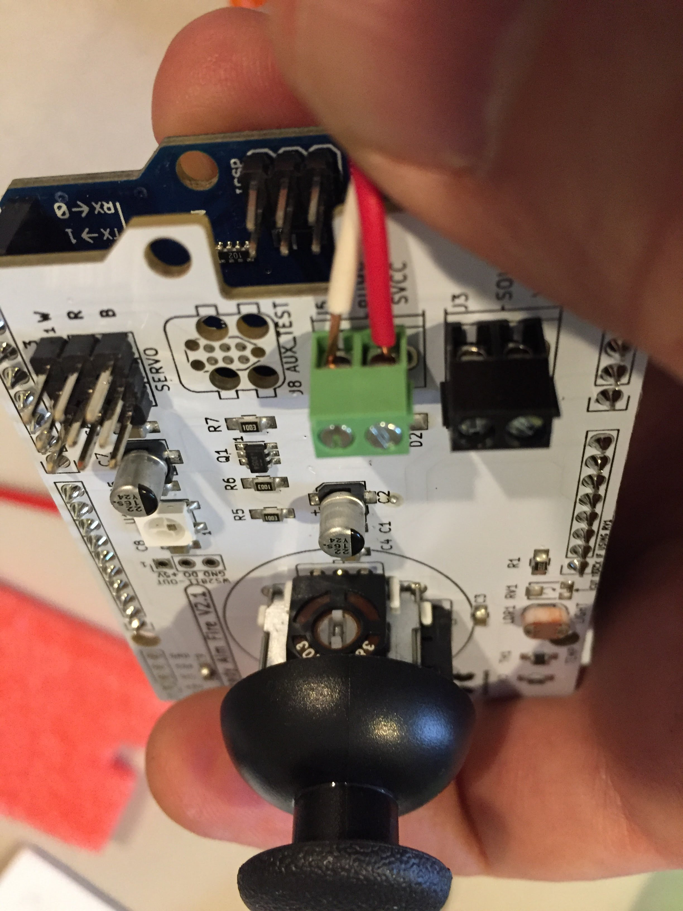
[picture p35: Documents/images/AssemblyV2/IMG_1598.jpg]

Repeat for the solenoid.
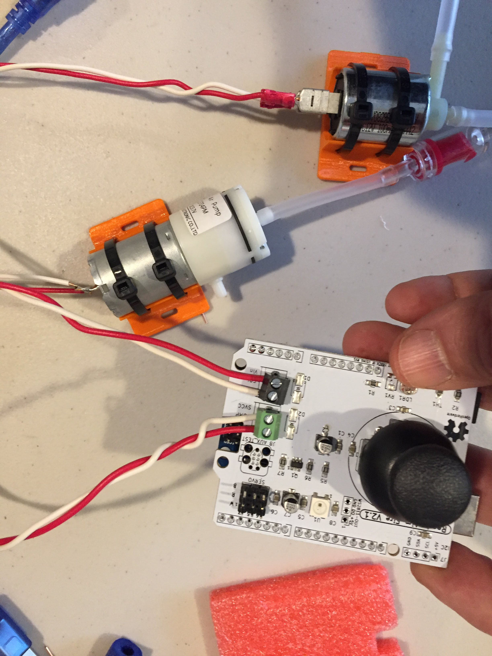
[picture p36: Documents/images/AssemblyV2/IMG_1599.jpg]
sol attach


Attach the Servo extension cables to the servo leads from the pan tilt mechanism. These are supplied to give you more flexibility in laying out your whole machine.
Line up the wires so they are similarly colored. In the example here, orange goes to white, red to red and brown to black.
(white is signal, Red is servo positive voltage, Black is Ground.) The middle one is alway voltage, and usually the darkest one is ground.
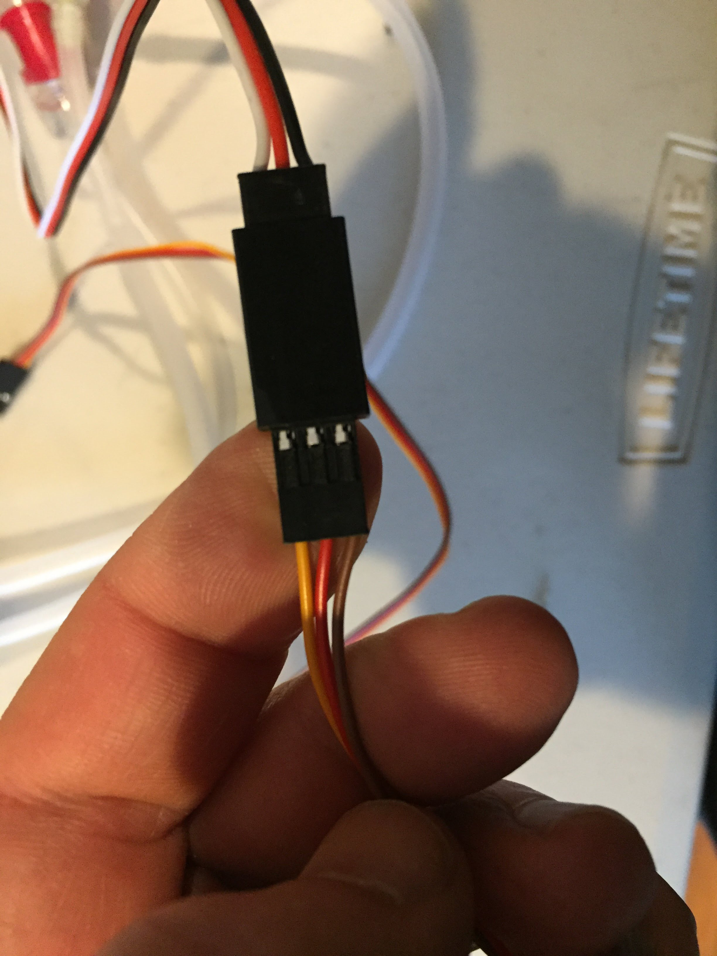
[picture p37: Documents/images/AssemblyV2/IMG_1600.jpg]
Servo Extensions

Attach the extension leads to the shield. Attach the bottom servo (azimuth) to the header labeled 3 (closest to the edge of the board) and the upper (elevation) servo to the header marked 5. Each header is also labeled on the side, W R B. Line these up to the Signal (W) Voltage (R) and GND (B). Note the female headers on the leads are oriented perpendicular to the long edge of the board.
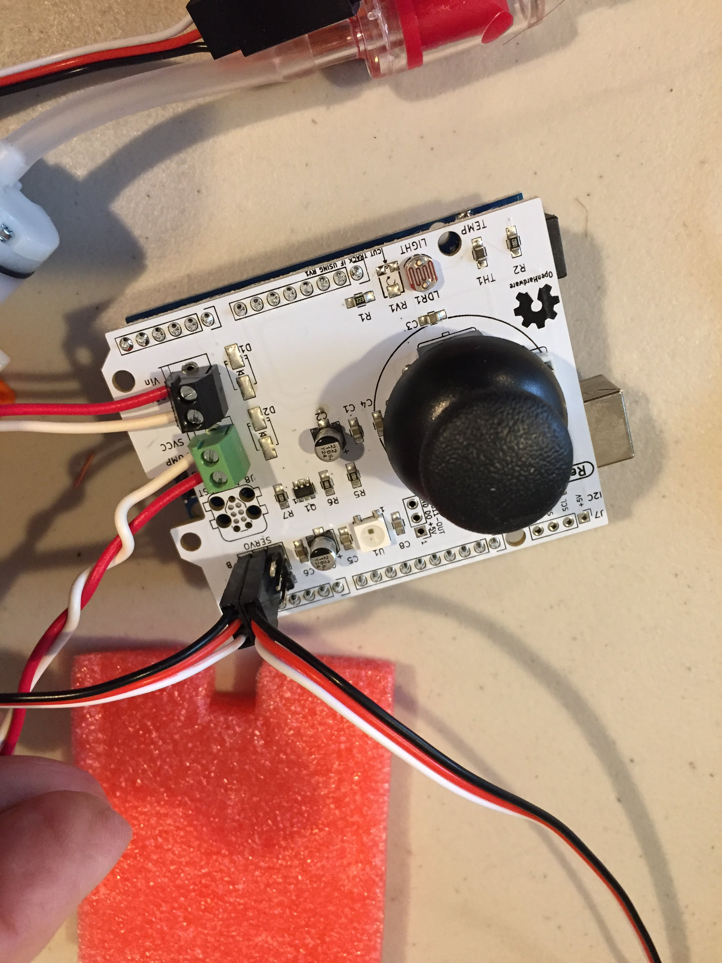
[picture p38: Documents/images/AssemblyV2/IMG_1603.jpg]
Servo Connections


## Make it easier to move around and keep together.
Now we'll fasten everything to the foam core. Lay out your components in a way you feel convenient. You don't have to match this picture. Later if you want to tidy even more you can adjust the lengths of the leads and tubing.
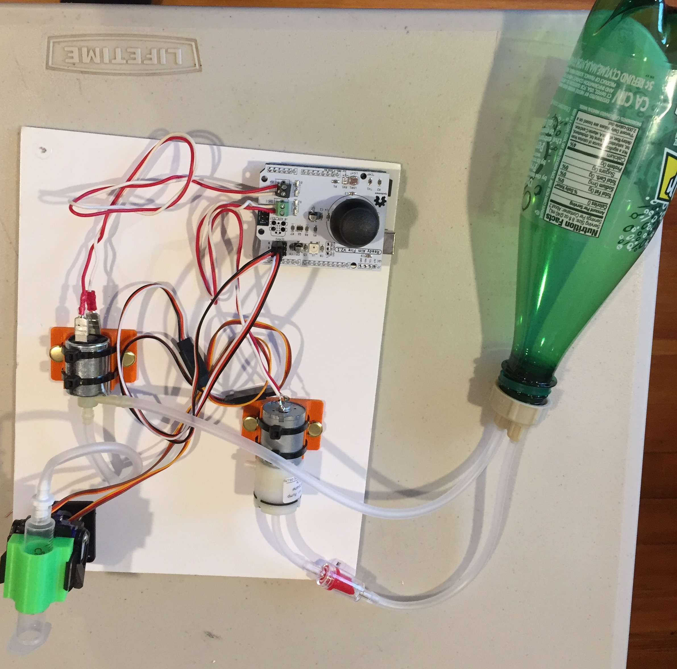
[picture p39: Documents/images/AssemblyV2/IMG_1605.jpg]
Final Assembly


You can use the brass paper fasteners to attach the 3D printed parts, and the two sided foam tape to attach the pan-tilt and the arduino.
The brass fasteners can be pushed through the holes and through the foam core. If you have trouble, you can pre-punch holes with an x-acto knife in the foam core.
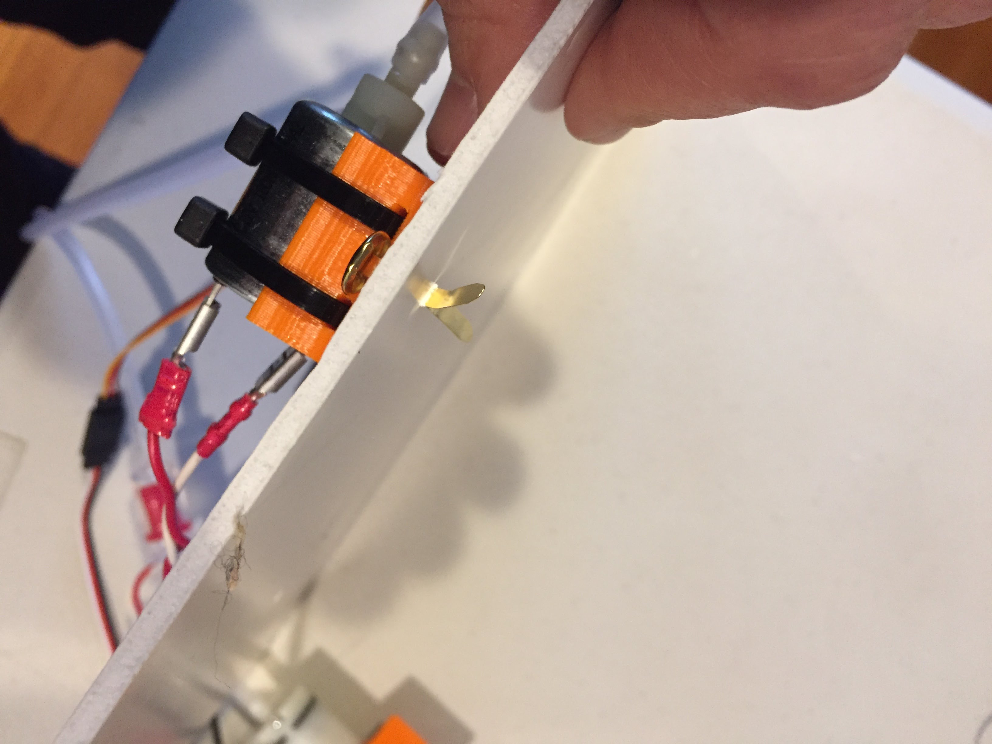
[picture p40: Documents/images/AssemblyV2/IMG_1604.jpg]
fasteners


And here's a closeup (the bottle is out of the pic) of the final assembly:
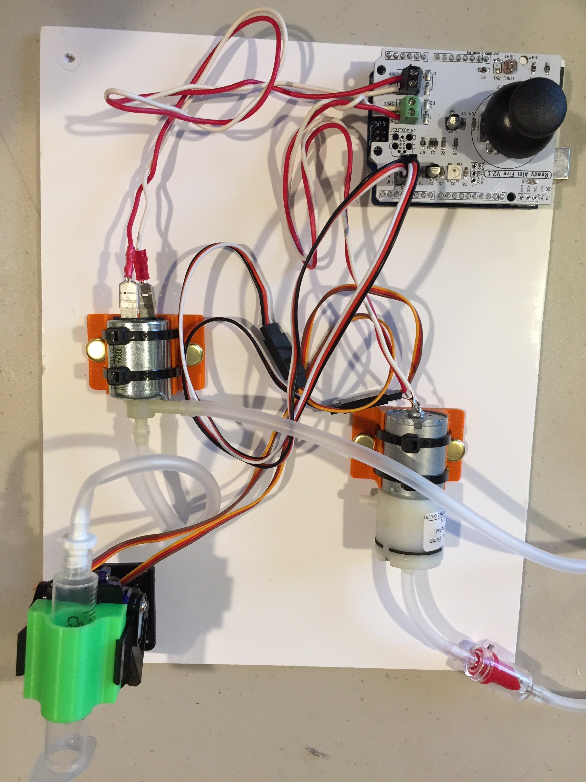
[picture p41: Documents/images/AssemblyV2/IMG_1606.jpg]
final-final


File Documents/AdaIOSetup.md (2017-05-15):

# Adafruit IO setup for SillyString shooter project
First get an account at Adafruit.com.
Then go to io.adafruit.com
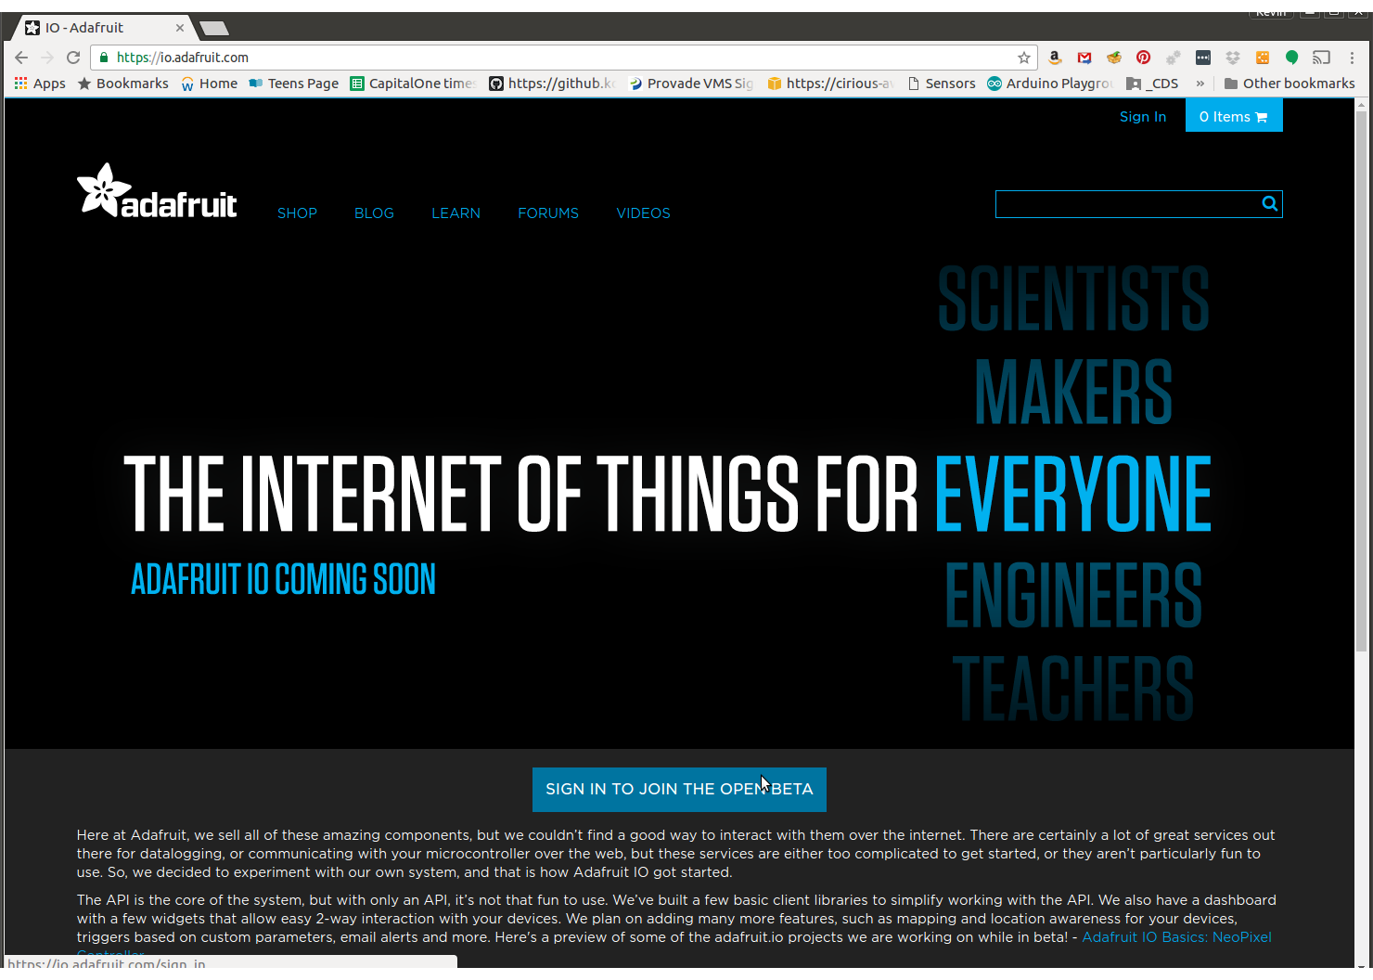
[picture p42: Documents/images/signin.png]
signin


You'll need to click joinbeta after signing in.
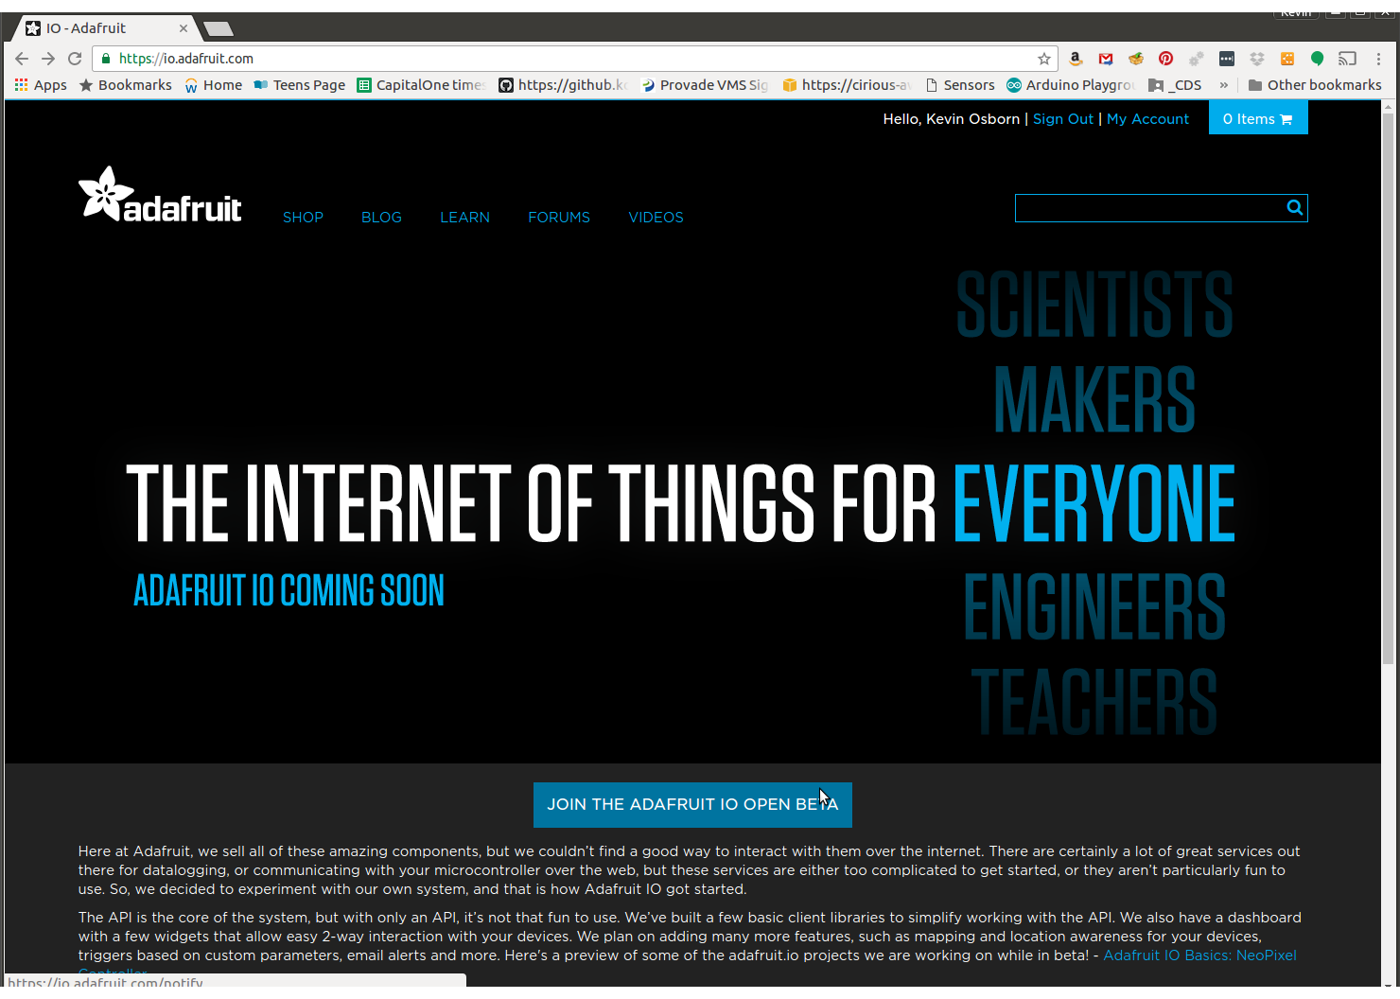
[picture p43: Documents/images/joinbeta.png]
joinbeta


This takes us to the default dashboard, navigate away by clickin on "Dashboards"
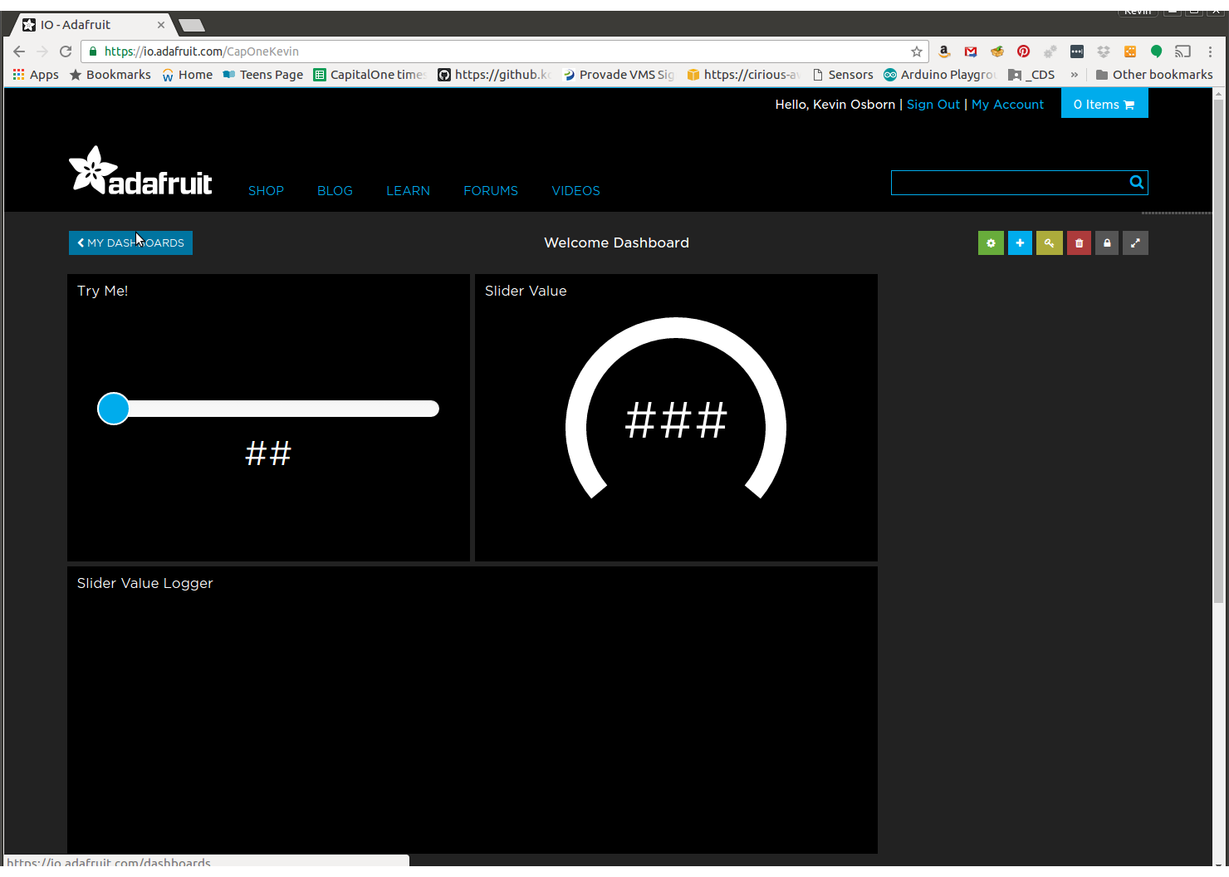
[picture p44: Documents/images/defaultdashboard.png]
defaultdashboard


Go to Your Feeds:
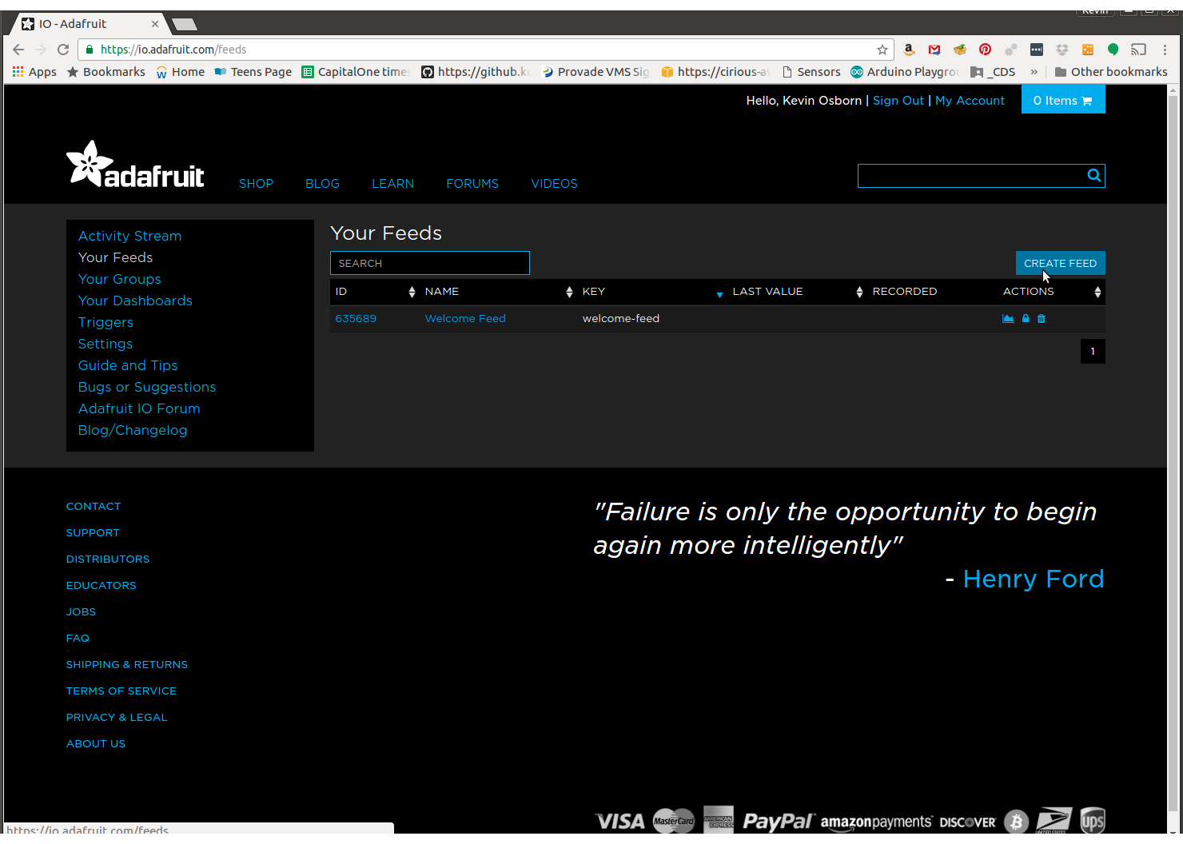
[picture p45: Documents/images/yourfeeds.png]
yourfeeds


Create a feed called SillyFire
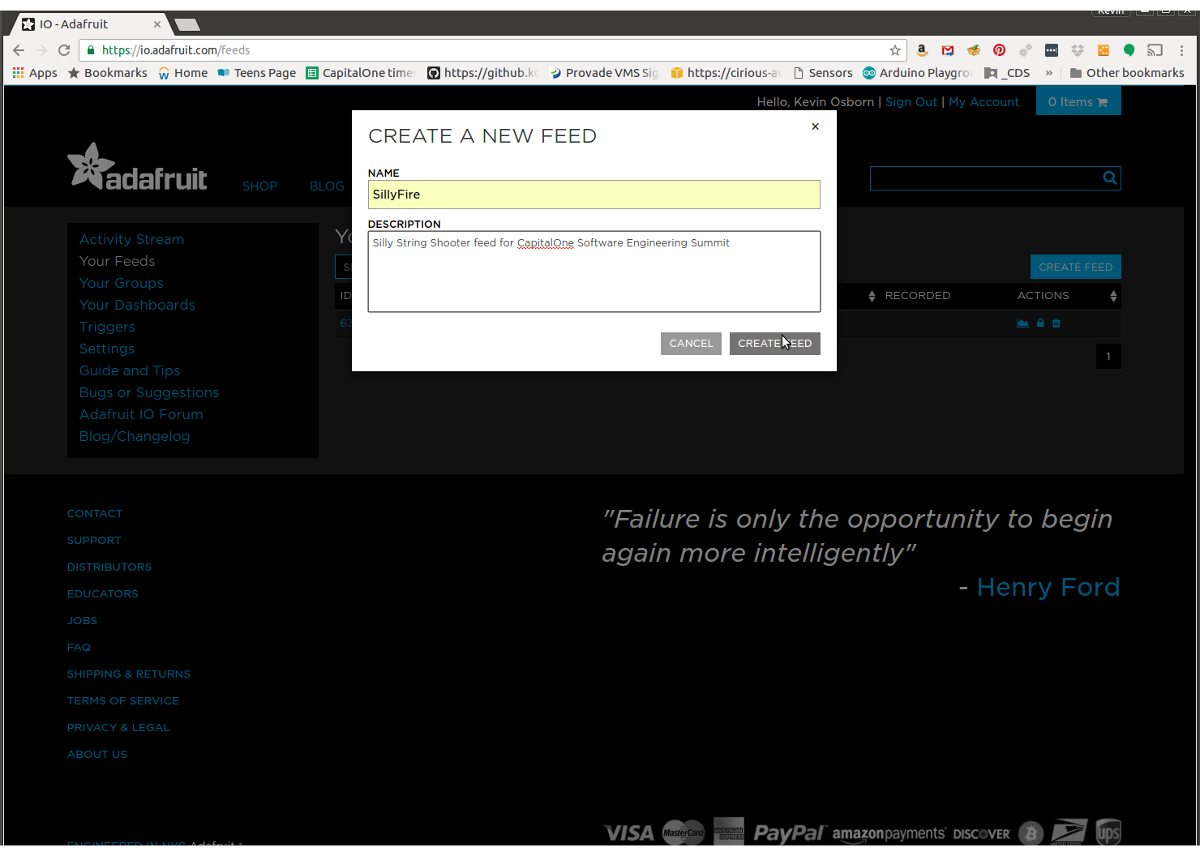
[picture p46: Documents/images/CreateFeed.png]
createfeed


Now go back to dashboards and create a new dashboard
Click on Create Dashboard
Once there, click on the plus to create a new block/control
The wizard will walk you through. You can also create new feeds here, but in our case, we'll select SillyFire.

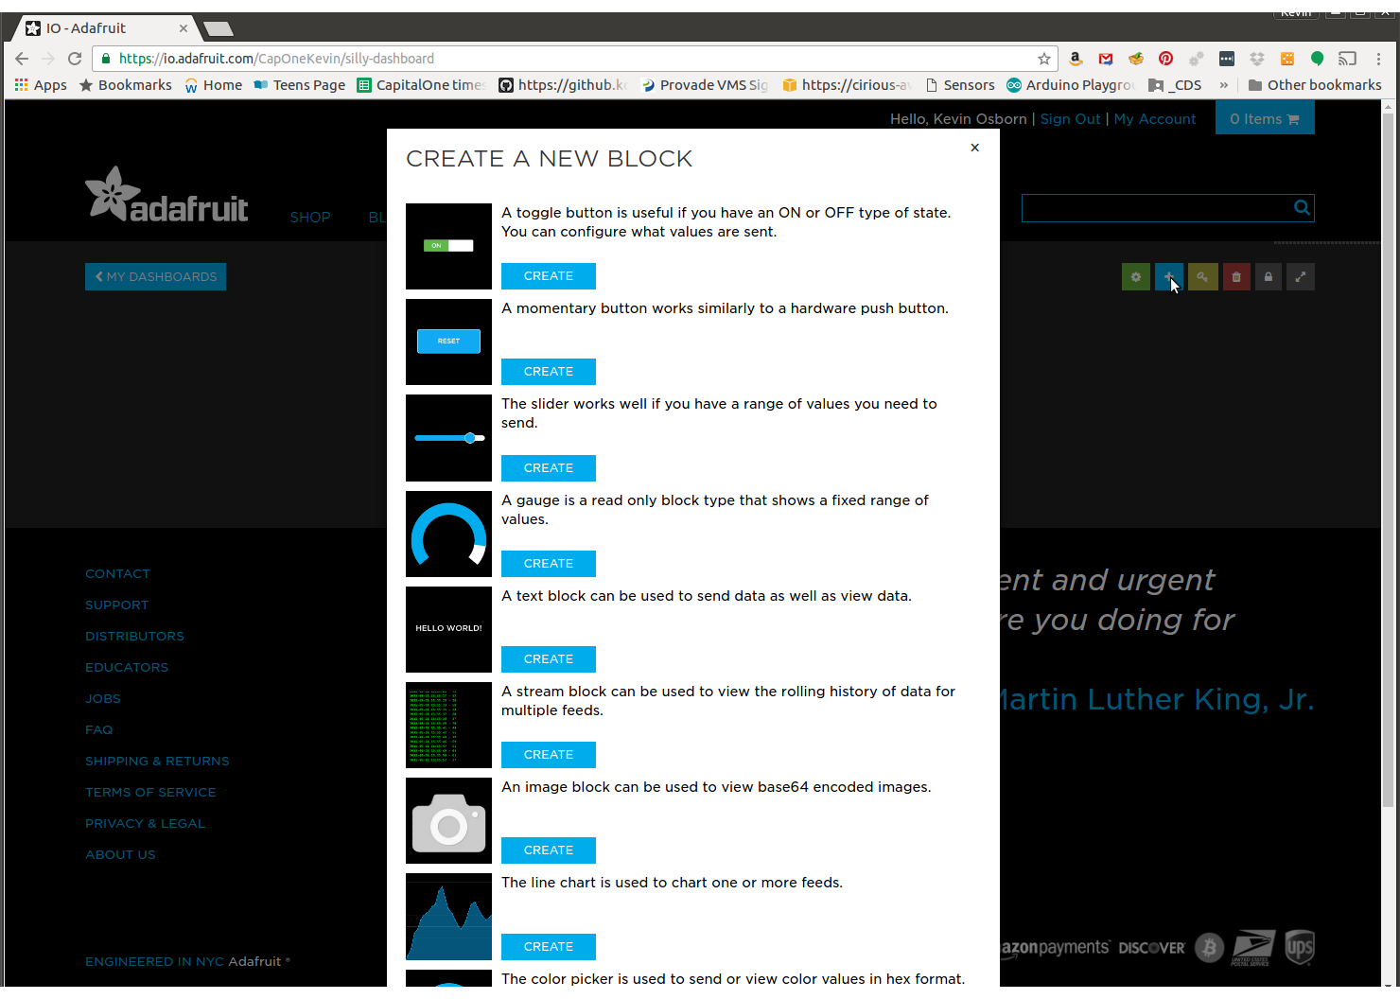
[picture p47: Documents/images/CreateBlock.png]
Createblock


Pick button, and make yourself a fire button
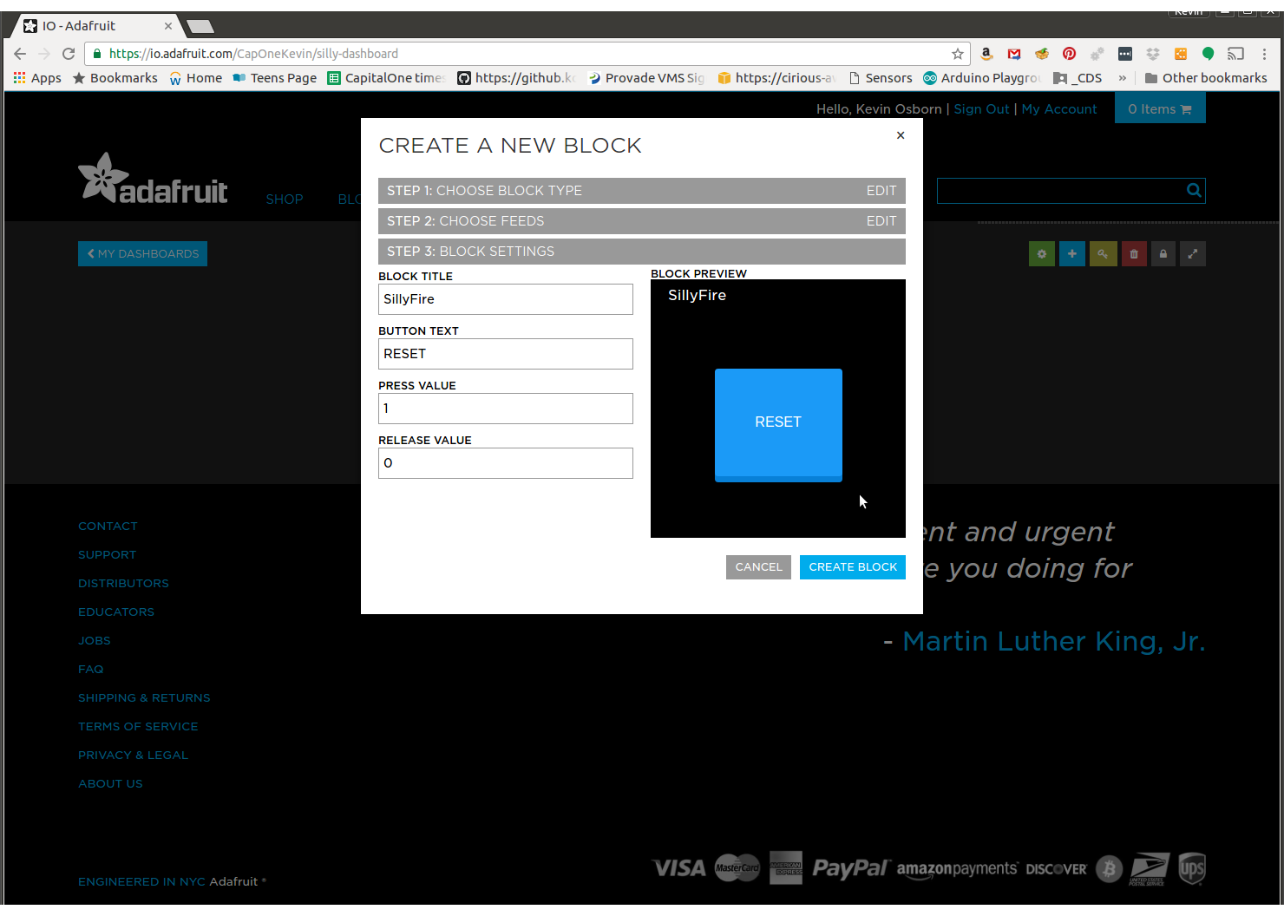
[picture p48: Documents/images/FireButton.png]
Firebutton


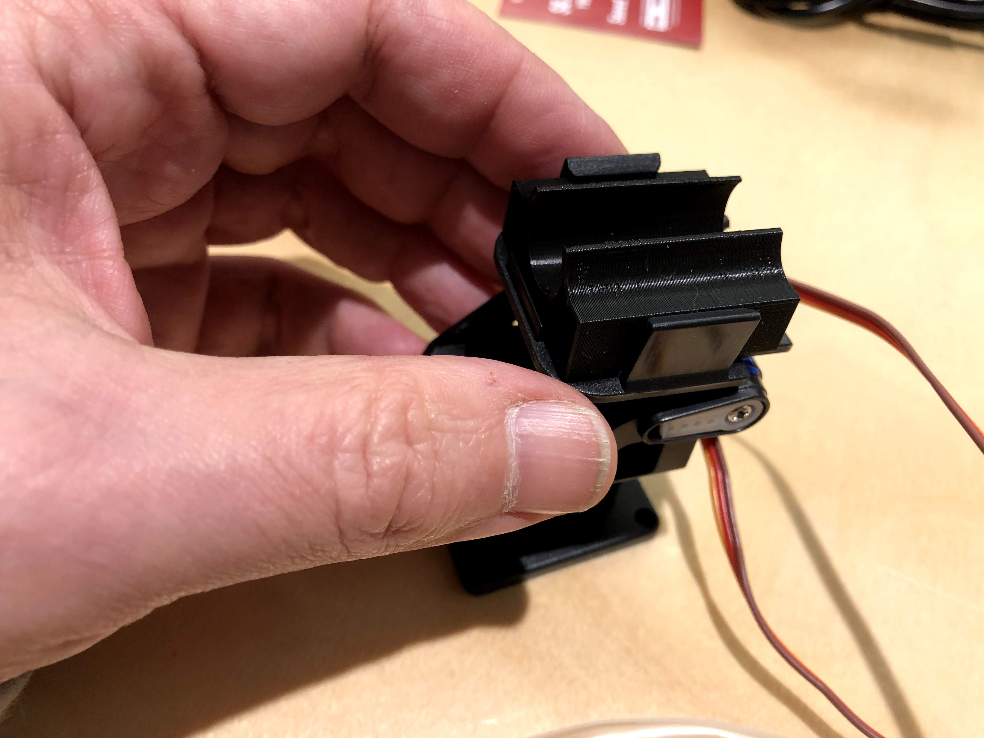
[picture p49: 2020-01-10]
Documents/images/AssemblyV3/IMG_2975.jpg

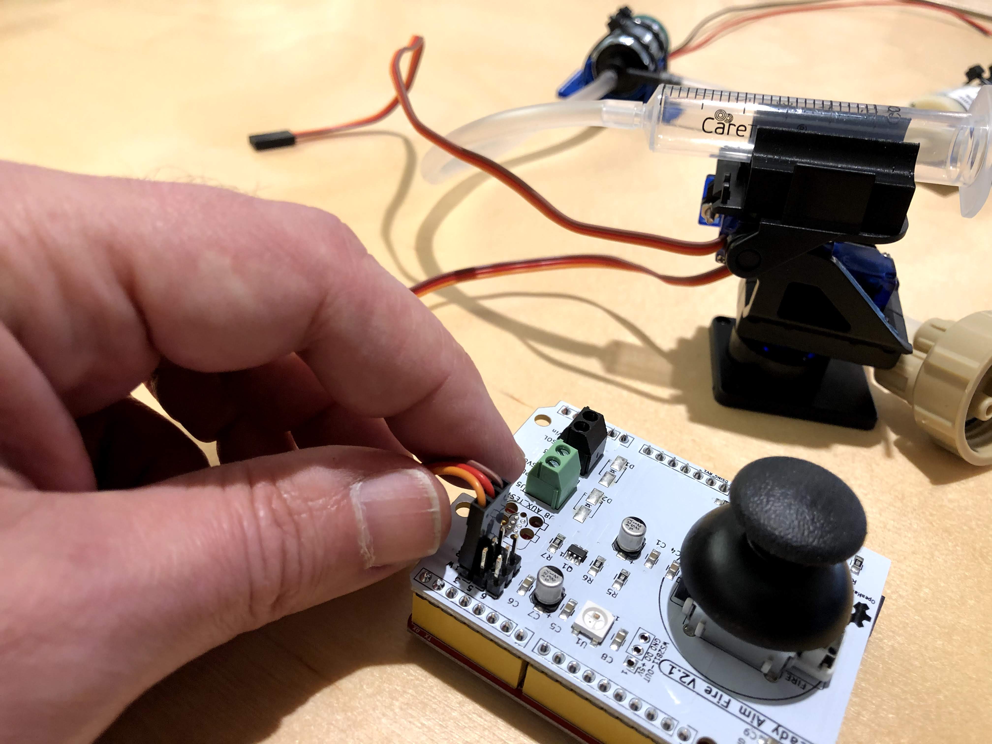
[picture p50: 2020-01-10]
Documents/images/AssemblyV3/IMG_2977.jpg

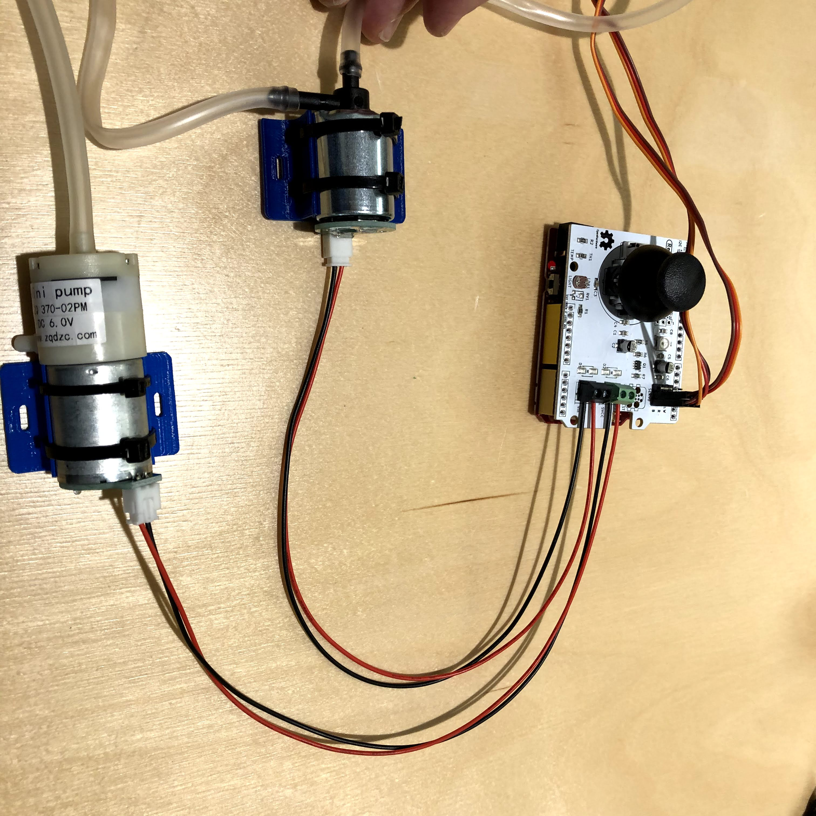
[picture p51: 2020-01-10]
Documents/images/AssemblyV3/IMG_2985.jpg

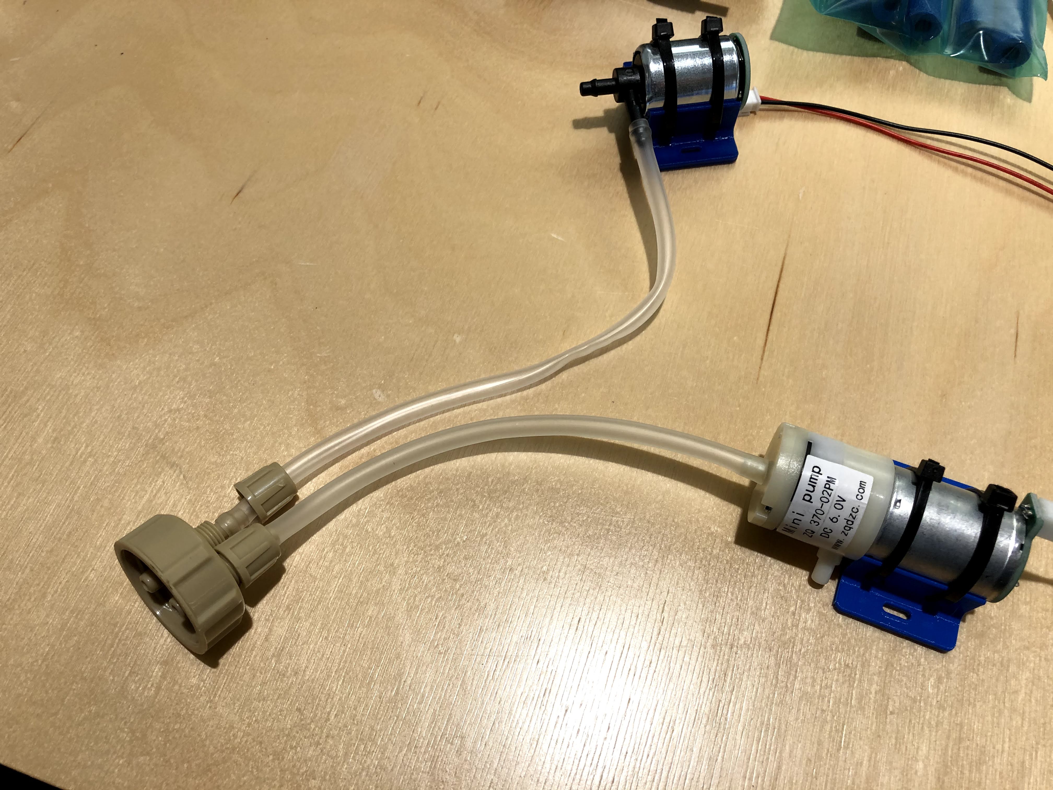
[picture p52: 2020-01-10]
Documents/images/AssemblyV3/IMG_2972.jpg

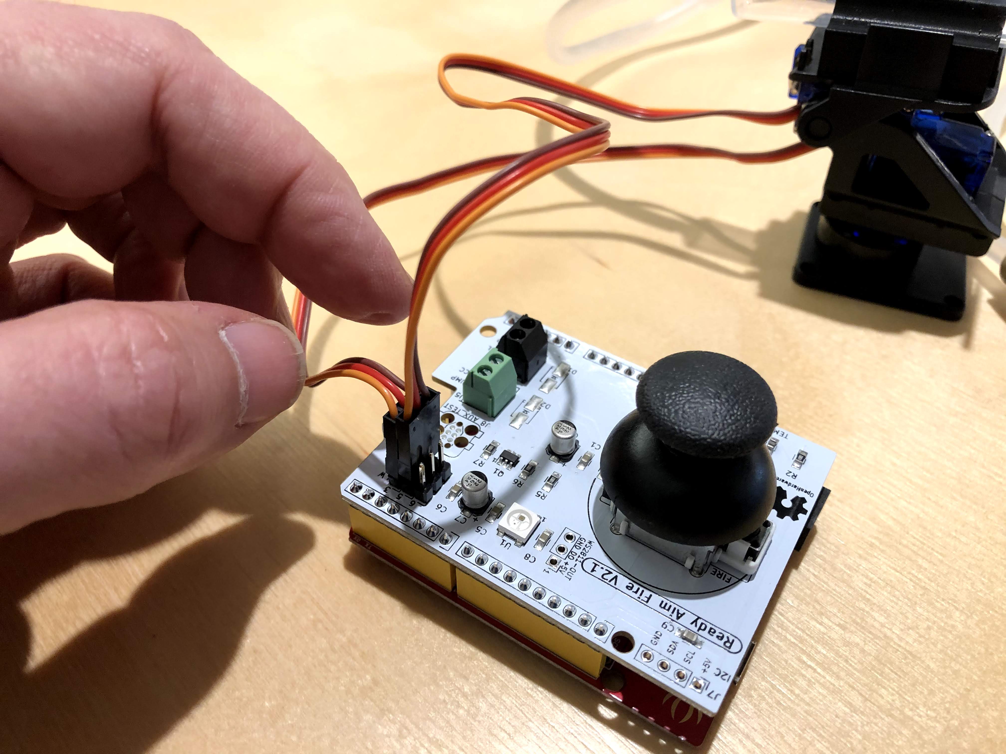
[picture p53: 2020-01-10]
Documents/images/AssemblyV3/IMG_2978.jpg

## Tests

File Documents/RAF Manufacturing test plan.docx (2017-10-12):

# RAF Manufacturing Test Plan

Version 1.0

Kevin Osborn

September 6, 2017

## Overview

The RAF (Ready Aim Fire) board is and Arduino shield intended for use with an Arduino Uno R3 or compatible board. It’s function is to implement an aimable foam dart shooter for software education purposes.

## Features

- 2 axis analog joystick for aiming a pan tilt mechanism
- Button (integrated in joystick) for firing or other IO purposes
- WS2812B Addressable RGB LED for feedback
- 3 servo headers (two for pan tilt and a spare) with separate 6V power supply for servos
- 2 Mosfet outputs
  - Switched VIN (preferably 9V > 1.5A) (used to drive gas solenoid valve for firing foam dart)
  - Servo VCC (6V) provided by onboard regulator (used to drive air pump)
- Temperature sensor (for analog input tutorials) - NTC thermistor wired as a voltage divider
- Light sensor (for gesture firing and analog input tutorials) - CDS LDR wired as a voltage divider
- Expansion connectors for additional WS2812B strips, and i2c sensors

# 1. Functions to be tested

  1.1. Joystick x and y reading
  1.2. Button Activation
  1.3. WS2812B function
  1.4. 6 V power supply
  1.5. Light sensor function
  1.6. Temp Sensor function
  1.7. 6V Mosfet output
  1.8. VIN Mosfet output

## 2. Method of test

  2.1. Test Equipment

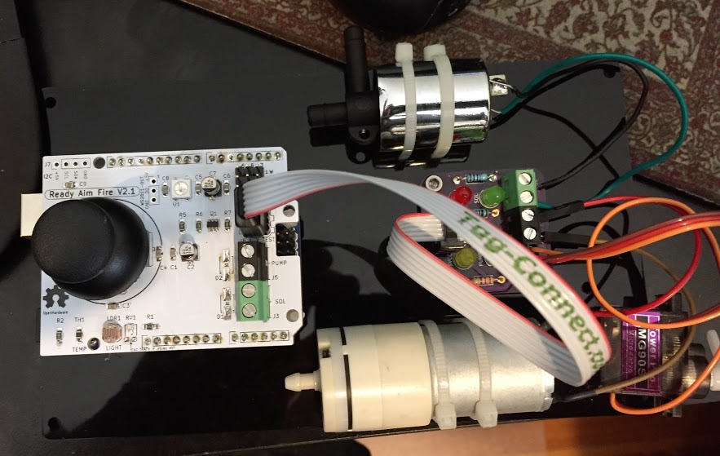
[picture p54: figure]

    2.1.1. Arduino loaded with test software
    2.1.2. Auxiliary analog power test board connected by ribbon cable to 6 pin test connector.
  2.2. Test Setup
    2.2.1. Connect the RAF shield to an Arduino Uno loaded with test software
    2.2.2. Connect Auxiliary power test board
    2.2.3. Apply VIN power
  2.3. Test Steps
    2.3.1. Verify that the VIN and 6V LEDs are lit on the Aux. board.

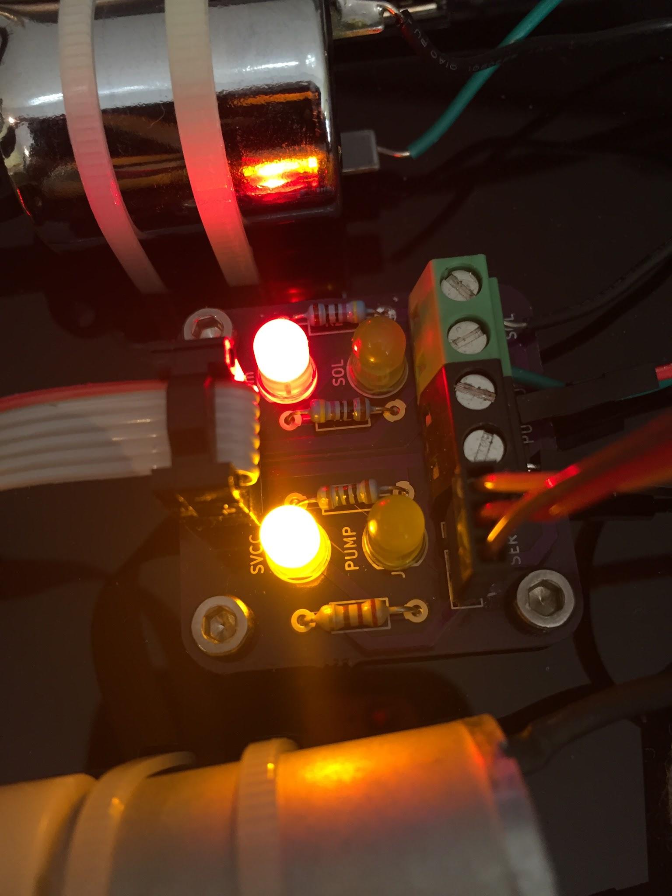
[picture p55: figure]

      2.3.1.1. LED-VIN OFF means short somewhere either at 6V LDO or Mosfet -- FAIL
      2.3.1.2. LED-6V OFF (and VIN on) means failure of 6V LDO - FAIL
      2.3.1.3. Both on - PASS
    2.3.2. Test 1 Verify that the WS2812B: Press the Joystick button (test number will flash blue)
      2.3.2.1. Not illuminated or white, bad WS2812B - FAIL
      2.3.2.2. Red, Green, Blue in sequence - PASS
    2.3.3. Test 2 Air pump: press joystick button (test number will flash blue)
      2.3.3.1. Air pump will come on for 1 sec. - PASS
      2.3.3.2. Weak or not on - Mosfet or LDO FAIL.
    2.3.4. Test 3 Solenoid: press joystick button (test number will flash blue)
      2.3.4.1. Solenoid will click 3 times - PASS
      2.3.4.2. If it doesn’t click, - Mosfet FAIL
    2.3.5. Test 4 Joystick test: click button (test number will flash blue)
      2.3.5.1. Move joystick to vertical and horizontal limits in both directions. LED will light Green on PASS
      2.3.5.2. If it doesn’t light green, FAIL. Abort test by clicking button
    2.3.6. Test 5 Temperature sensor: click joystick button.(test number will flash blue)
      2.3.6.1. Touch TH1 with finger. If led turns green, PASS (detects slight rise in temp.)
      2.3.6.2. If it doesn’t turn green FAIL (or adjust firmware parameters) abort test by pushing button
    2.3.7. Test 6 Light sensor: push joystick button (test number will flash blue)
      2.3.7.1. Wave hand over light sensor, LED should turn green.
      2.3.7.2. If it doesn’t turn green FAIL (or adjust firmware parameters) abort test by pushing button
    2.3.8. Test 7 Servo test: press Joystick button (test number will flash blue)
      2.3.8.1. Servo should move - PASS
      2.3.8.2. No movment - LDO or arduino FAIL

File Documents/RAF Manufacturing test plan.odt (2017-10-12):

RAF Manufacturing Test Plan

Version 1.0

Kevin Osborn

September 6, 2017

Overview

The RAF (Ready Aim Fire) board is and Arduino shield intended for use with an Arduino Uno R3 or compatible board. It’s function is to implement an aimable foam dart shooter for software education purposes.

Features

- 2 axis analog joystick for aiming a pan tilt mechanism
- Button (integrated in joystick) for firing or other IO purposes
- WS2812B Addressable RGB LED for feedback
- 3 servo headers (two for pan tilt and a spare) with separate 6V power supply for servos
- 2 Mosfet outputs
  - Switched VIN (preferably 9V > 1.5A) (used to drive gas solenoid valve for firing foam dart)
  - Servo VCC (6V) provided by onboard regulator (used to drive air pump)
- Temperature sensor (for analog input tutorials) - NTC thermistor wired as a voltage divider
- Light sensor (for gesture firing and analog input tutorials) - CDS LDR wired as a voltage divider
- Expansion connectors for additional WS2812B strips, and i2c sensors
1. Functions to be tested
  1. Joystick x and y reading
  2. Button Activation
  3. WS2812B function
  4. 6 V power supply
  5. Light sensor function
  6. Temp Sensor function
  7. 6V Mosfet output
  8. VIN Mosfet output
2. Method of test
  1. Test Equipment


    1. Arduino loaded with test software
    2. Auxiliary analog power test board connected by ribbon cable to 6 pin test connector.
  2. Test Setup
    1. Connect the RAF shield to an Arduino Uno loaded with test software
    2. Connect Auxiliary power test board
    3. Apply VIN power
  3. Test Steps
    1. Verify that the VIN and 6V LEDs are lit on the Aux. board.


      1. LED-VIN OFF means short somewhere either at 6V LDO or Mosfet -- FAIL
      2. LED-6V OFF (and VIN on) means failure of 6V LDO - FAIL
      3. Both on - PASS
    2. Test 1 Verify that the WS2812B: Press the Joystick button (test number will flash blue)
      1. Not illuminated or white, bad WS2812B - FAIL
      2. Red, Green, Blue in sequence - PASS
    3. Test 2 Air pump: press joystick button (test number will flash blue)
      1. Air pump will come on for 1 sec. - PASS
      2. Weak or not on - Mosfet or LDO FAIL.
    4. Test 3 Solenoid: press joystick button (test number will flash blue)
      1. Solenoid will click 3 times - PASS
      2. If it doesn’t click, - Mosfet FAIL
    5. Test 4 Joystick test: click button (test number will flash blue)
      1. Move joystick to vertical and horizontal limits in both directions. LED will light Green on PASS
      2. If it doesn’t light green, FAIL. Abort test by clicking button
    6. Test 5 Temperature sensor: click joystick button.(test number will flash blue)
      1. Touch TH1 with finger. If led turns green, PASS (detects slight rise in temp.)
      2. If it doesn’t turn green FAIL (or adjust firmware parameters) abort test by pushing button
    7. Test 6 Light sensor: push joystick button (test number will flash blue)
      1. Wave hand over light sensor, LED should turn green.
      2. If it doesn’t turn green FAIL (or adjust firmware parameters) abort test by pushing button
    8. Test 7 Servo test: press Joystick button (test number will flash blue)
      1. Servo should move - PASS
      2. No movment - LDO or arduino FAIL

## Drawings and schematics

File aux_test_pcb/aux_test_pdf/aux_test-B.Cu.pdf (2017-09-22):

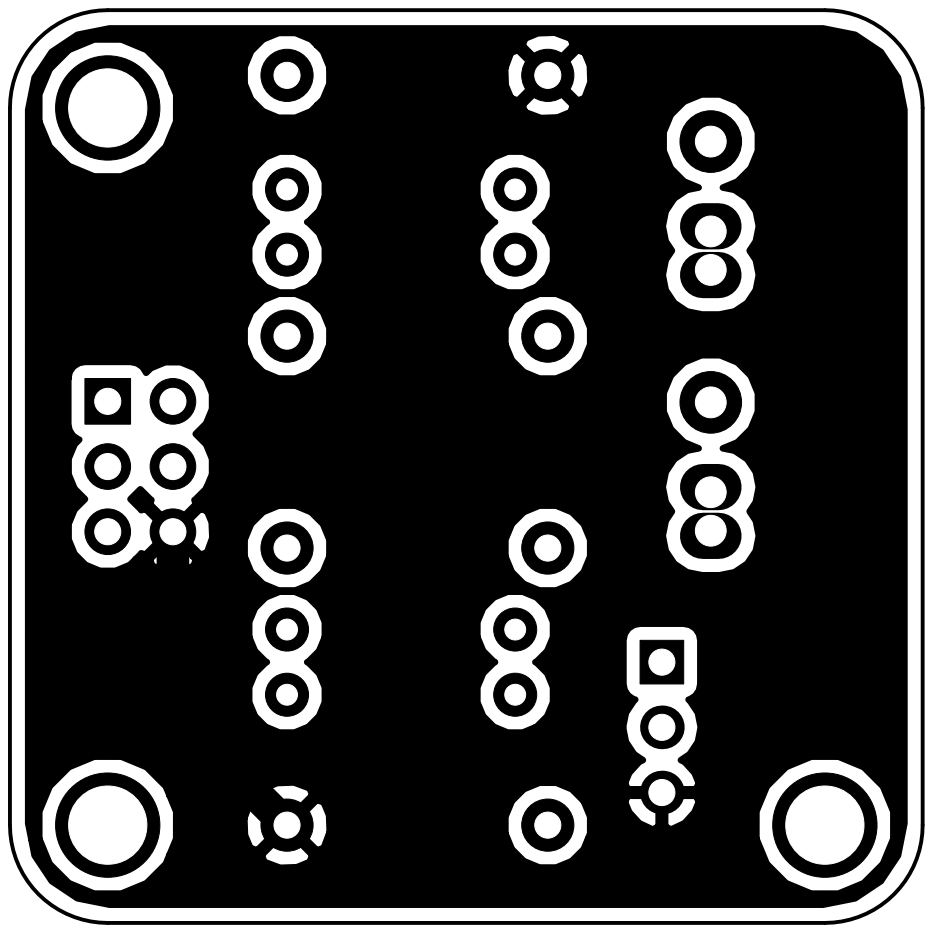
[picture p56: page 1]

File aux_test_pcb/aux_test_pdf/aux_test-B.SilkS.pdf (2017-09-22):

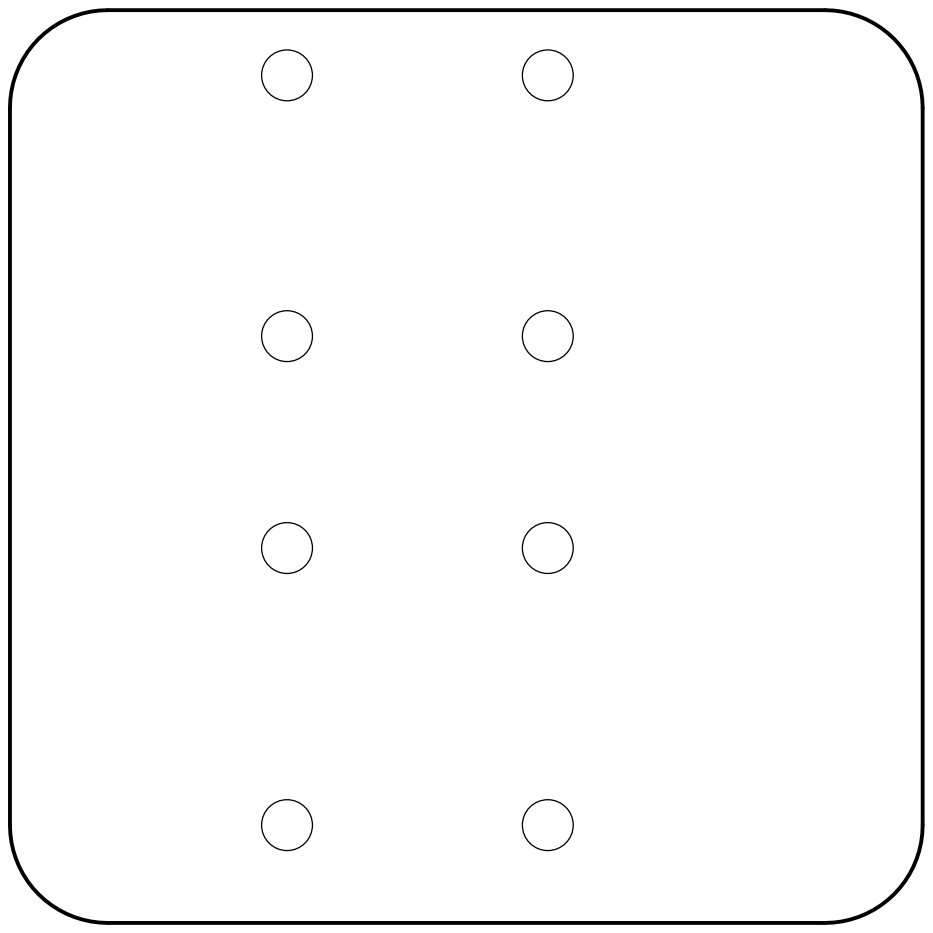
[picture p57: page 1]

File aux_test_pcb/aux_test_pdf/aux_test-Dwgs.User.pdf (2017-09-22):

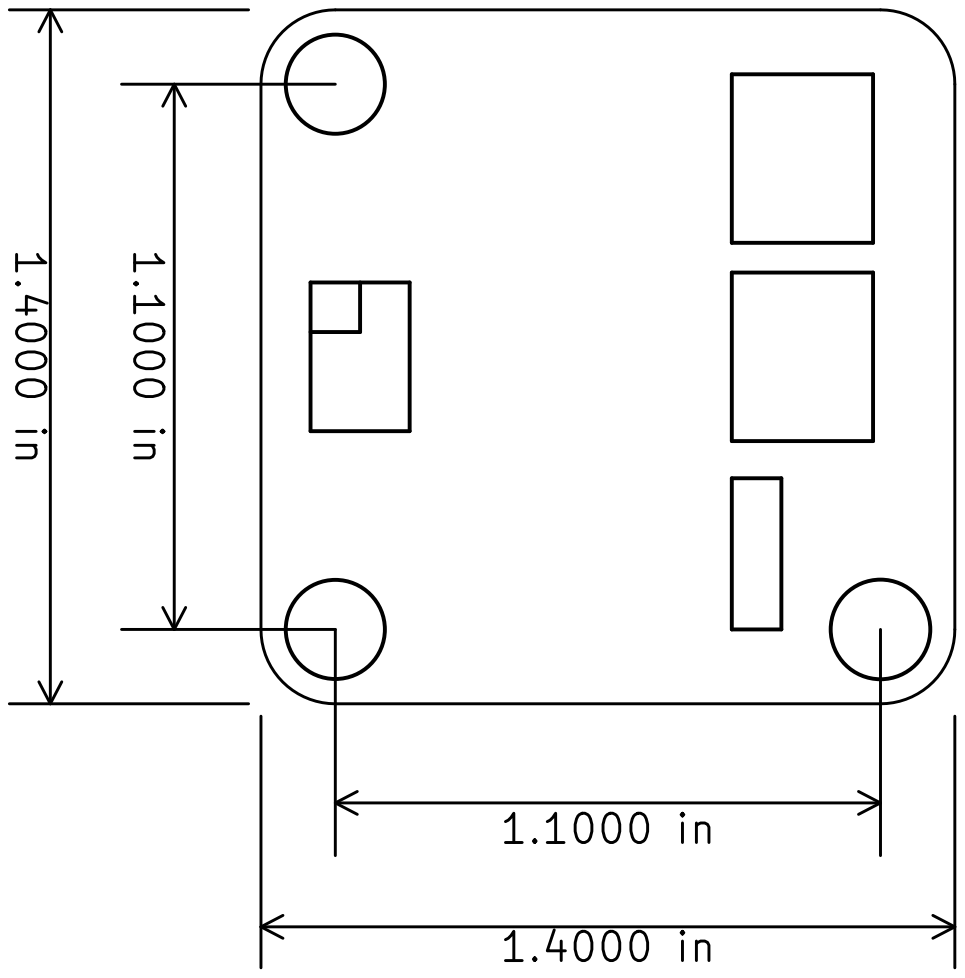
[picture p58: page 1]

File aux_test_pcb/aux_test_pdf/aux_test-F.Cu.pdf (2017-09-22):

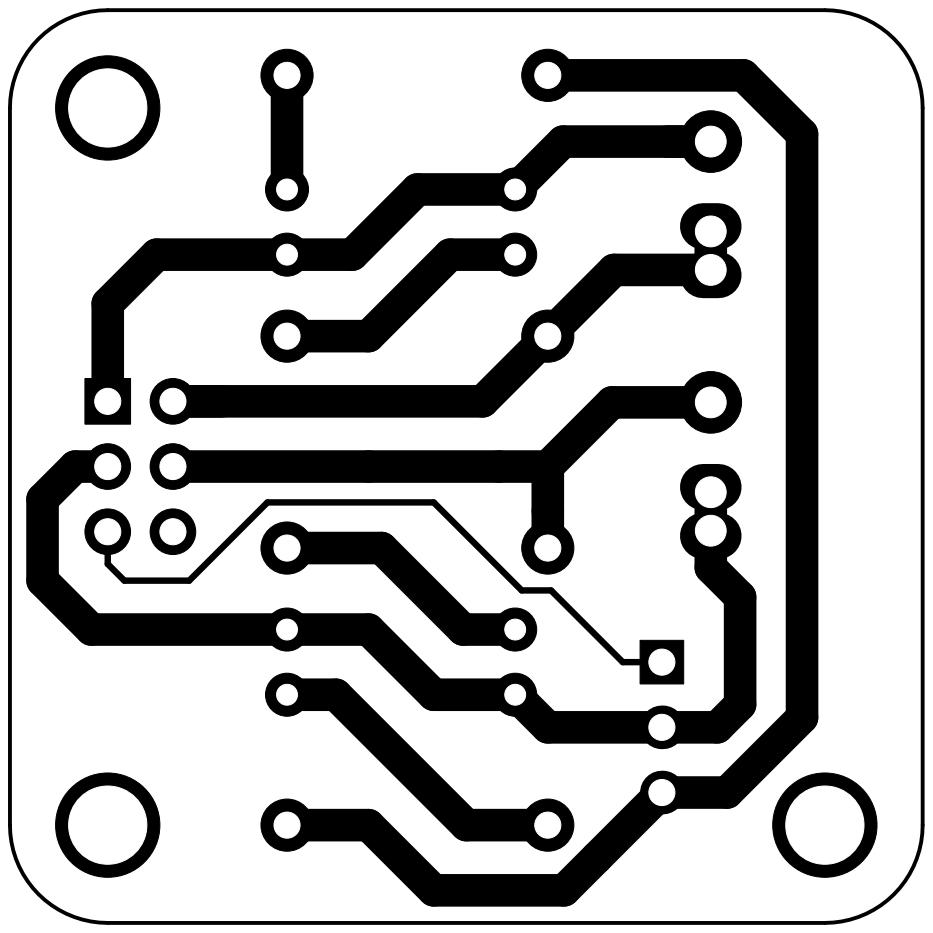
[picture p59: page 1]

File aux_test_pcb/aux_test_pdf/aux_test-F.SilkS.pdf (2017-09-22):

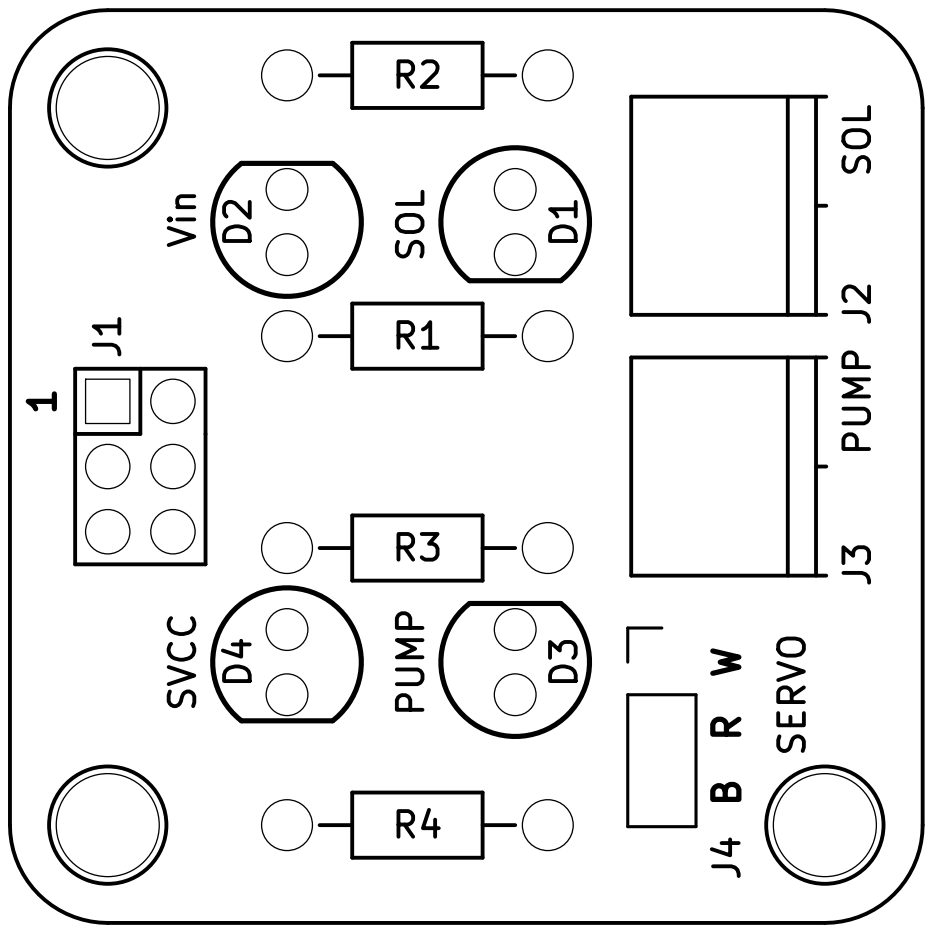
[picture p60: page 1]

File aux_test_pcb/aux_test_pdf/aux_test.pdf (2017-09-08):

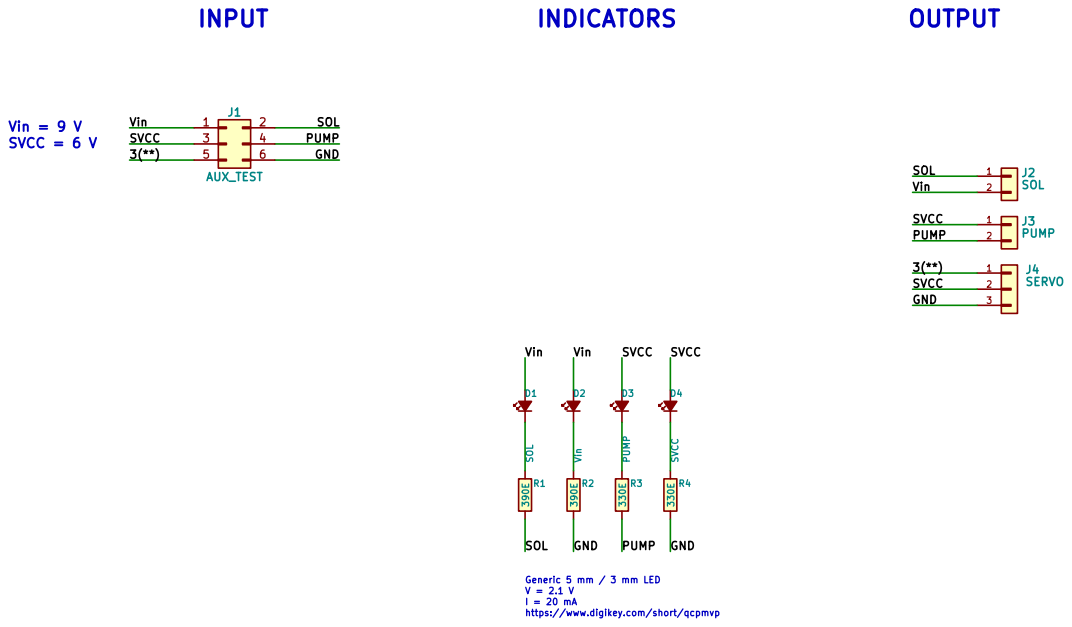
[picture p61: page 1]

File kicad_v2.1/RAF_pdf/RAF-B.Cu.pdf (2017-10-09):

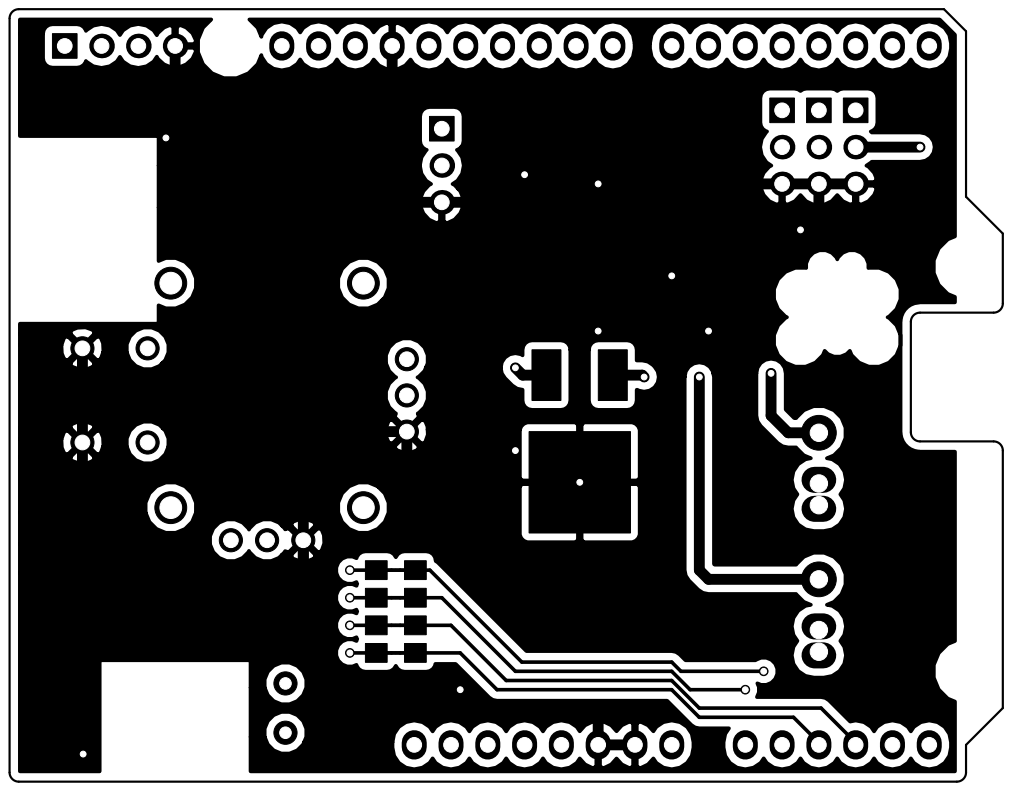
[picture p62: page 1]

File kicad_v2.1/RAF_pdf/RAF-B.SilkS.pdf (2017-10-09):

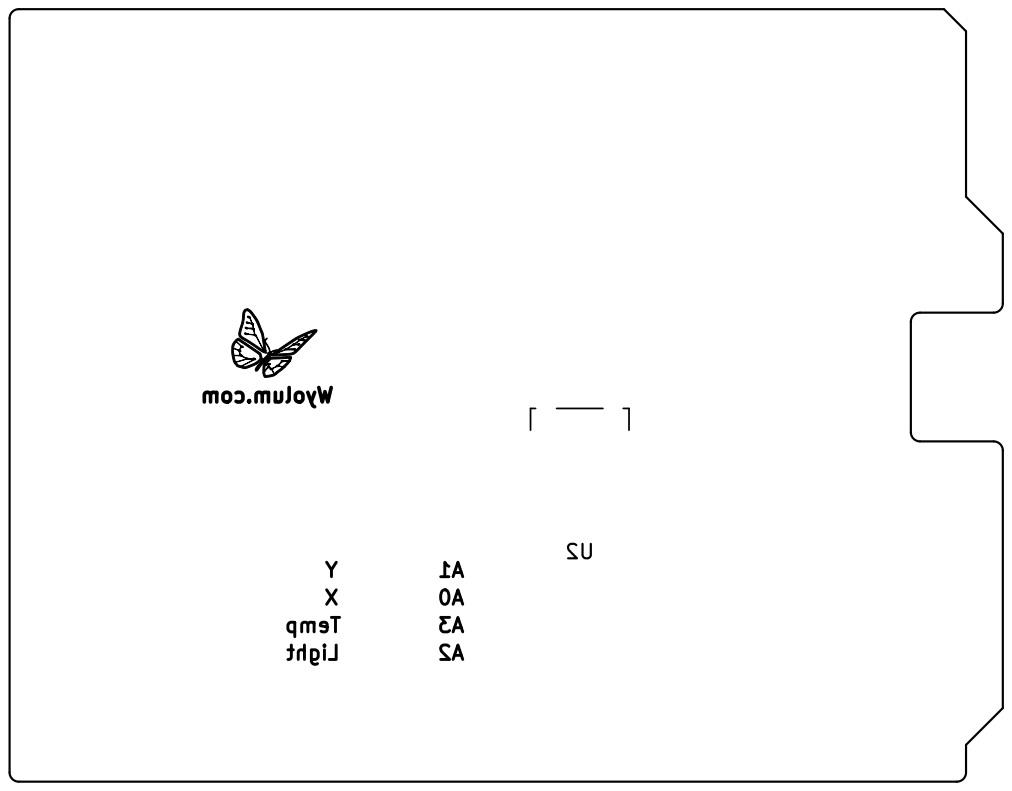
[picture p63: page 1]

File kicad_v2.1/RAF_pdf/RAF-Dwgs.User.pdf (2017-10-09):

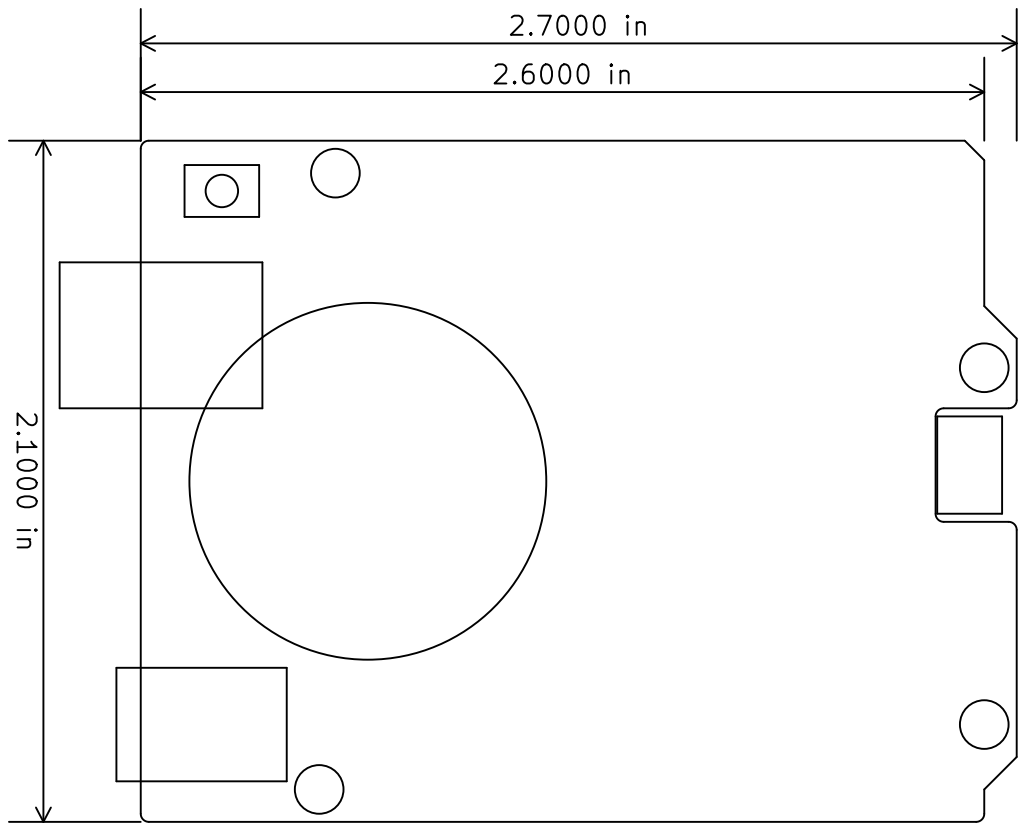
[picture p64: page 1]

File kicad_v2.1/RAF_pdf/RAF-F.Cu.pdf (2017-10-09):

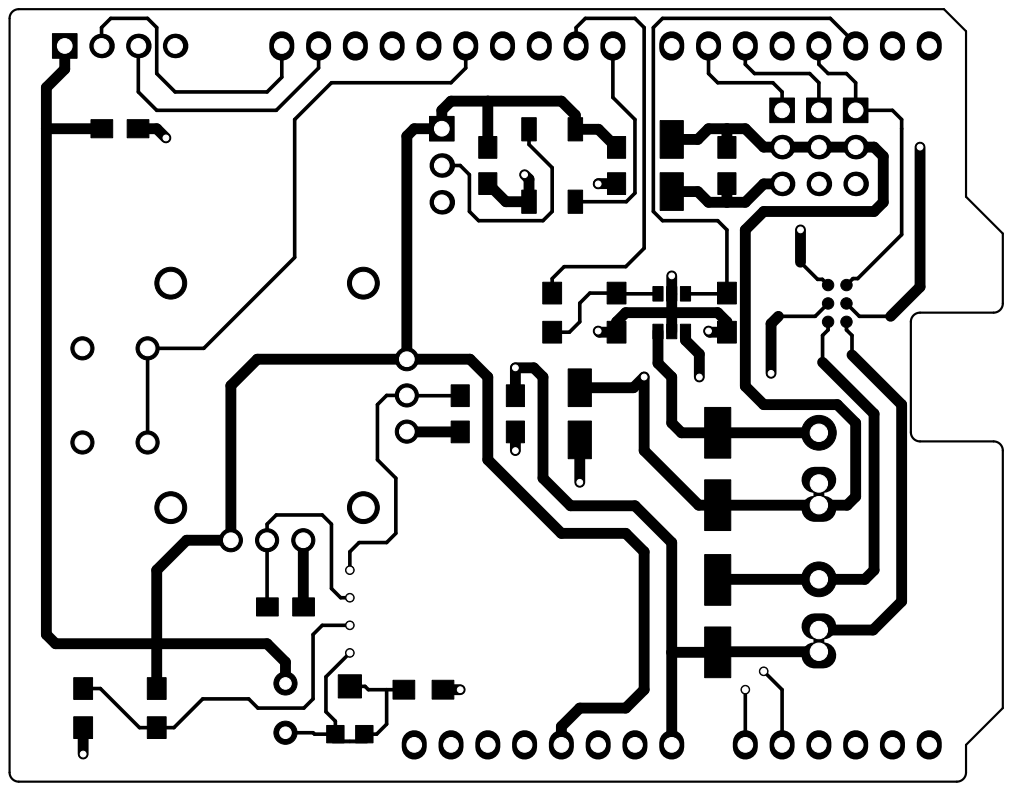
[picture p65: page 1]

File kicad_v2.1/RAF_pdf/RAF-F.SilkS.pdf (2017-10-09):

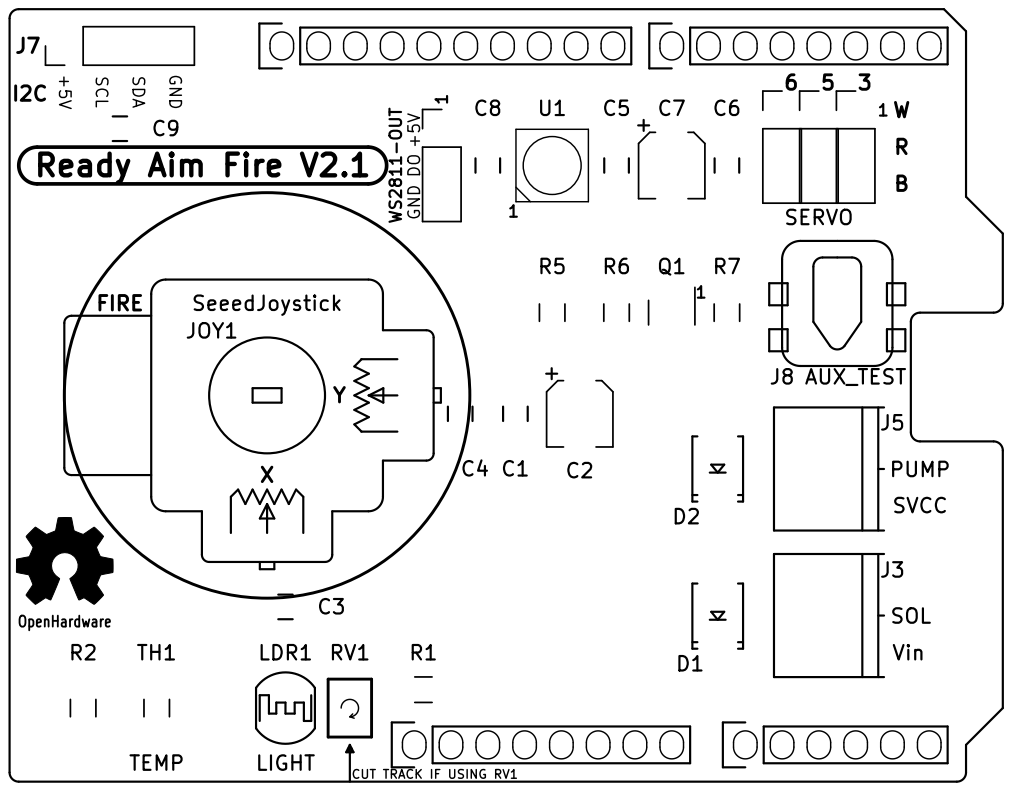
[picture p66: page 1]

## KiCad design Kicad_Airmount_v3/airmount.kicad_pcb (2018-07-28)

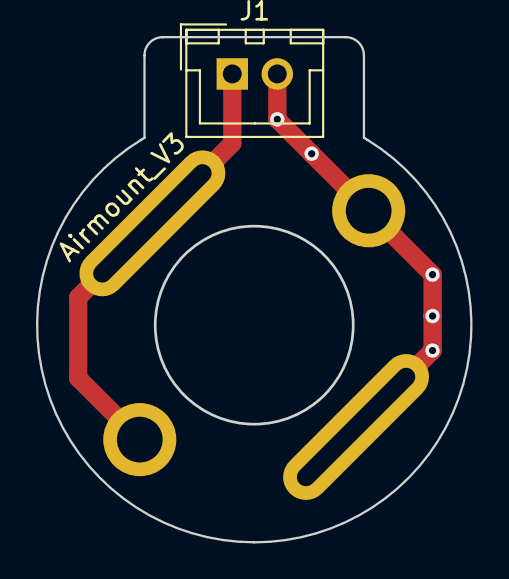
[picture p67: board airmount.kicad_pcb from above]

Board: 2 copper layers, 24.1 x 28.1 mm, 4 parts (0 on the bottom side), 2 nets.

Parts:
Board1: pumpBoard2
J1: JST; JST_XH_B02B-XH-A_02x2.50mm_Straight
M1: Motor_DC; p_contacts2
M2: Motor_DC; GasSolenoid2

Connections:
GND: J1.2, M1.2, M2.2
unnamed: J1.1, M1.1, M2.1

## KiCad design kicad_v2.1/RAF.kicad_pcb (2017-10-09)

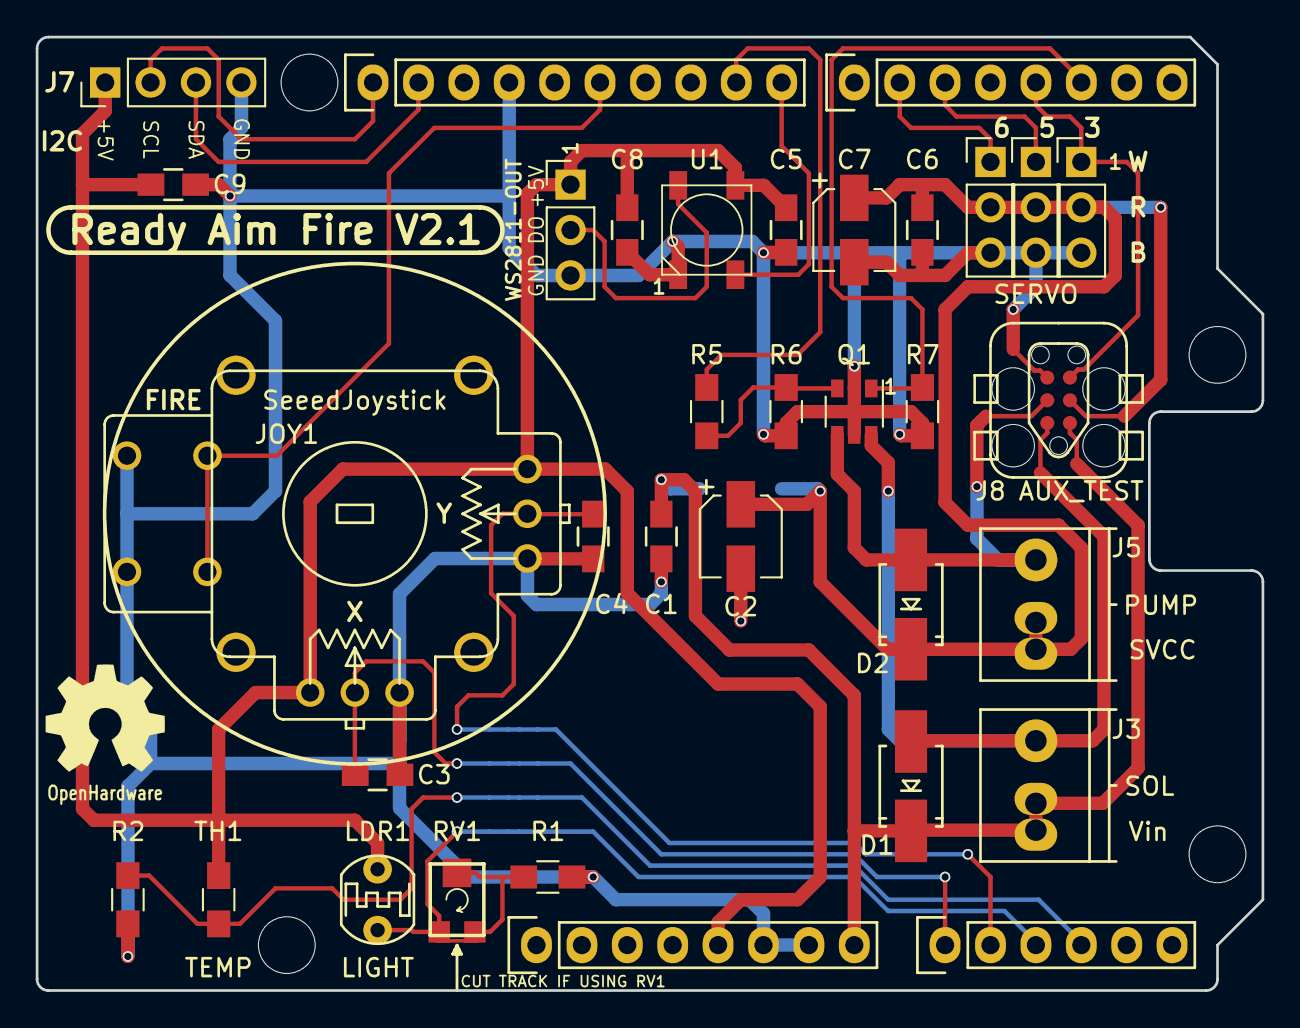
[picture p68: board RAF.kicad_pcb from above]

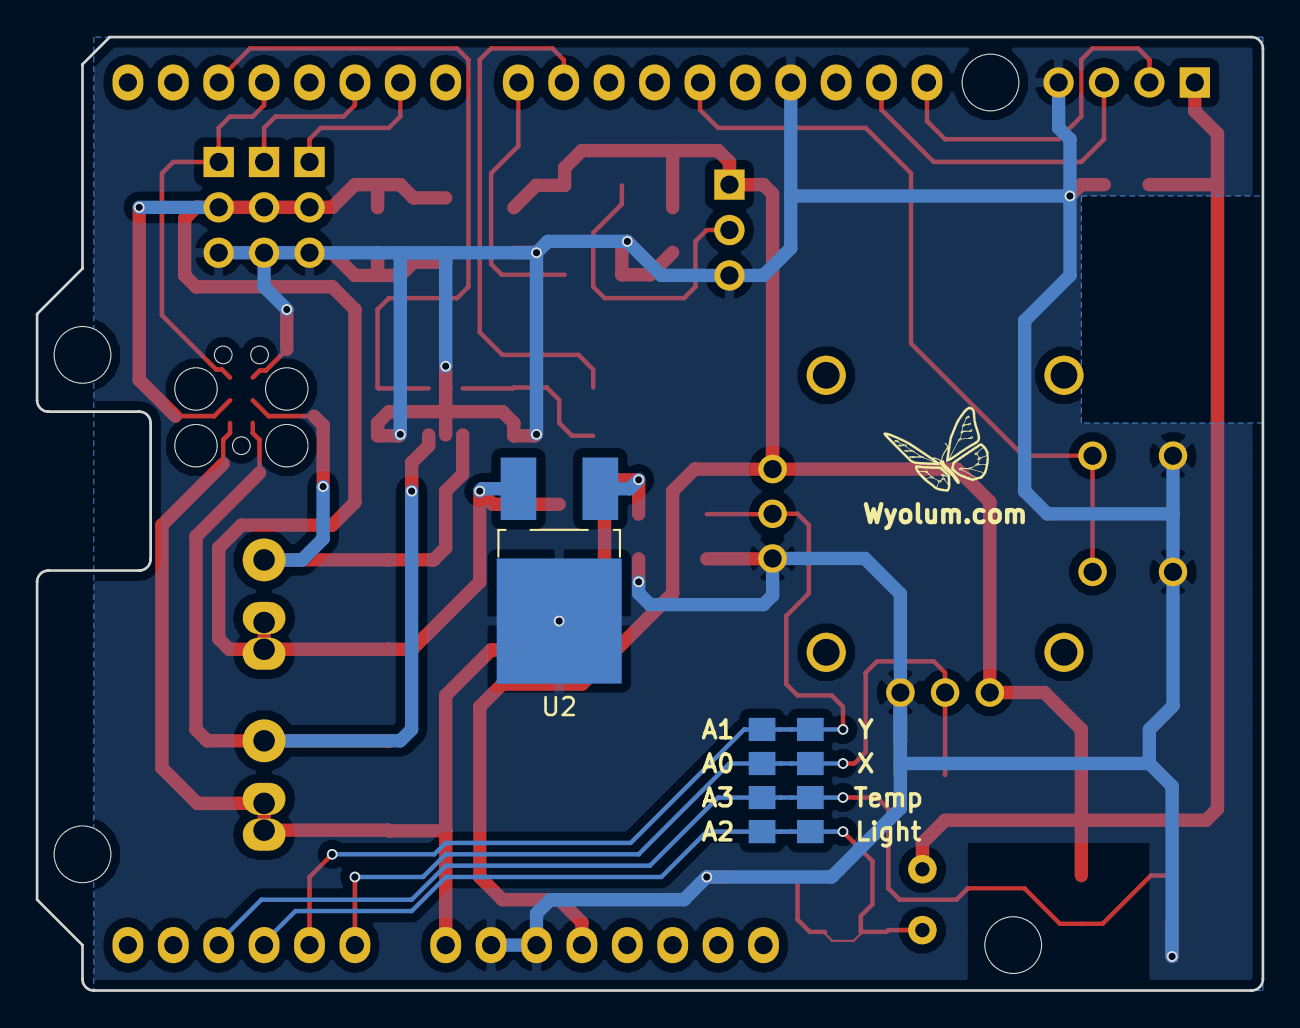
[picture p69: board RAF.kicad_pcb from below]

Board: 2 copper layers, 68.6 x 53.3 mm, 45 parts (6 on the bottom side), 21 nets.

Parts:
C1, C3, C4, C5, C6, C8, C9: 0.1uF; C_0805_HandSoldering
C2, C7: 22uF; CP_Elec_4x5.7
D1, D2: S1ATR; SMA_Handsoldering
H1, H2, H3, H4: NPTH_hole; NPTH_hole_3mm
J1, J2, J4: SERVO; Pin_Header_Straight_1x03_Pitch2.54mm
J3: SOL; TerminalBlock_Pheonix_PT-5.0mm_2pol
J5: PUMP; TerminalBlock_Pheonix_PT-5.0mm_2pol
J6: WS2811-OUT; Pin_Header_Straight_1x03_Pitch2.54mm
J7: I2C; Pin_Header_Straight_1x04_Pitch2.54mm
J8: AUX_TEST; TC2030-IDC
JOY1: SeeedJoystick; SEEED-Joystick_v2
JP1, JP2, JP3, JP4: Jumper_NC_Small; 0805_jumper
LDR1: LIGHT; Resistor_LDR_5.0x3.4
OSHW1: OSHW; OSHW_6mm
P1: Power; Socket_Strip_Arduino_1x08
P2: Analog; Socket_Strip_Arduino_1x06
P3: Digital; Socket_Strip_Arduino_1x10
P4: Digital; Socket_Strip_Arduino_1x08
Q1: FDC6305N; SuperSOT-6
R1: 22K; R_0805_HandSoldering
R2: 10K; R_0805_HandSoldering
R5, R6, R7: 100k; R_0805_HandSoldering
RV1: 100k; Res_variable
TH1: TEMP; R_0805_HandSoldering
U1: RGB_WS2811B; LED_WS2812B-PLCC4
U2: LF60CDT; DPak
WYO1: LOGO_WL; logo_wyo_butterfly_small

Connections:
+5V: C5.1, C8.1, C9.1, J6.1, J7.1, JOY1.X+, JOY1.Y+, LDR1.1, P1.5, TH1.1, U1.1
/2: P4.6, Q1.1, R7.2
/3(**): J1.1, J8.5, P4.5
/5(**): J2.1, P4.3
/6(**): J4.1, P4.2
/8: P3.10, U1.4
/9(**): P3.9, R5.2
/12(MISO): JOY1.B1, JOY1.B2, P3.6
/A0: C3.1, JOY1.X, JP1.1, JP1.2, P2.1
/A1: C4.1, JOY1.Y, JP2.1, JP2.2, P2.2
/A2: JP3.1, JP3.2, LDR1.2, P2.3, R1.1, RV1.1, RV1.2, RV1.3
/A3: JP4.1, JP4.2, P2.4, R2.1, TH1.2
/A4(SDA): J7.3, P3.2
/A5(SCL): J7.2, P3.1
/LED_OUT: J6.2, U1.2
/PUMP: D2.2, J5.2, J8.4, Q1.4
/SOL: D1.2, J3.2, J8.2, Q1.6
/SVCC: C2.1, C6.1, C7.1, D2.1, J1.2, J2.2, J4.2, J5.1, J8.3, U2.VO
/Vin: C1.1, D1.1, J3.1, J8.1, P1.8, U2.VI
GND: C1.2, C2.2, C3.2, C4.2, C5.2, C6.2, C7.2, C8.2, C9.2, J1.3, J2.3, J4.3, J6.3, J7.4, J8.6, JOY1.A1, JOY1.A2, JOY1.X-, JOY1.Y-, P1.6, P1.7, P3.4, Q1.2, Q1.5, R1.2, R2.2, R6.1, R7.1, U1.3, U2.GND
unnamed: Q1.3, R5.1, R6.2

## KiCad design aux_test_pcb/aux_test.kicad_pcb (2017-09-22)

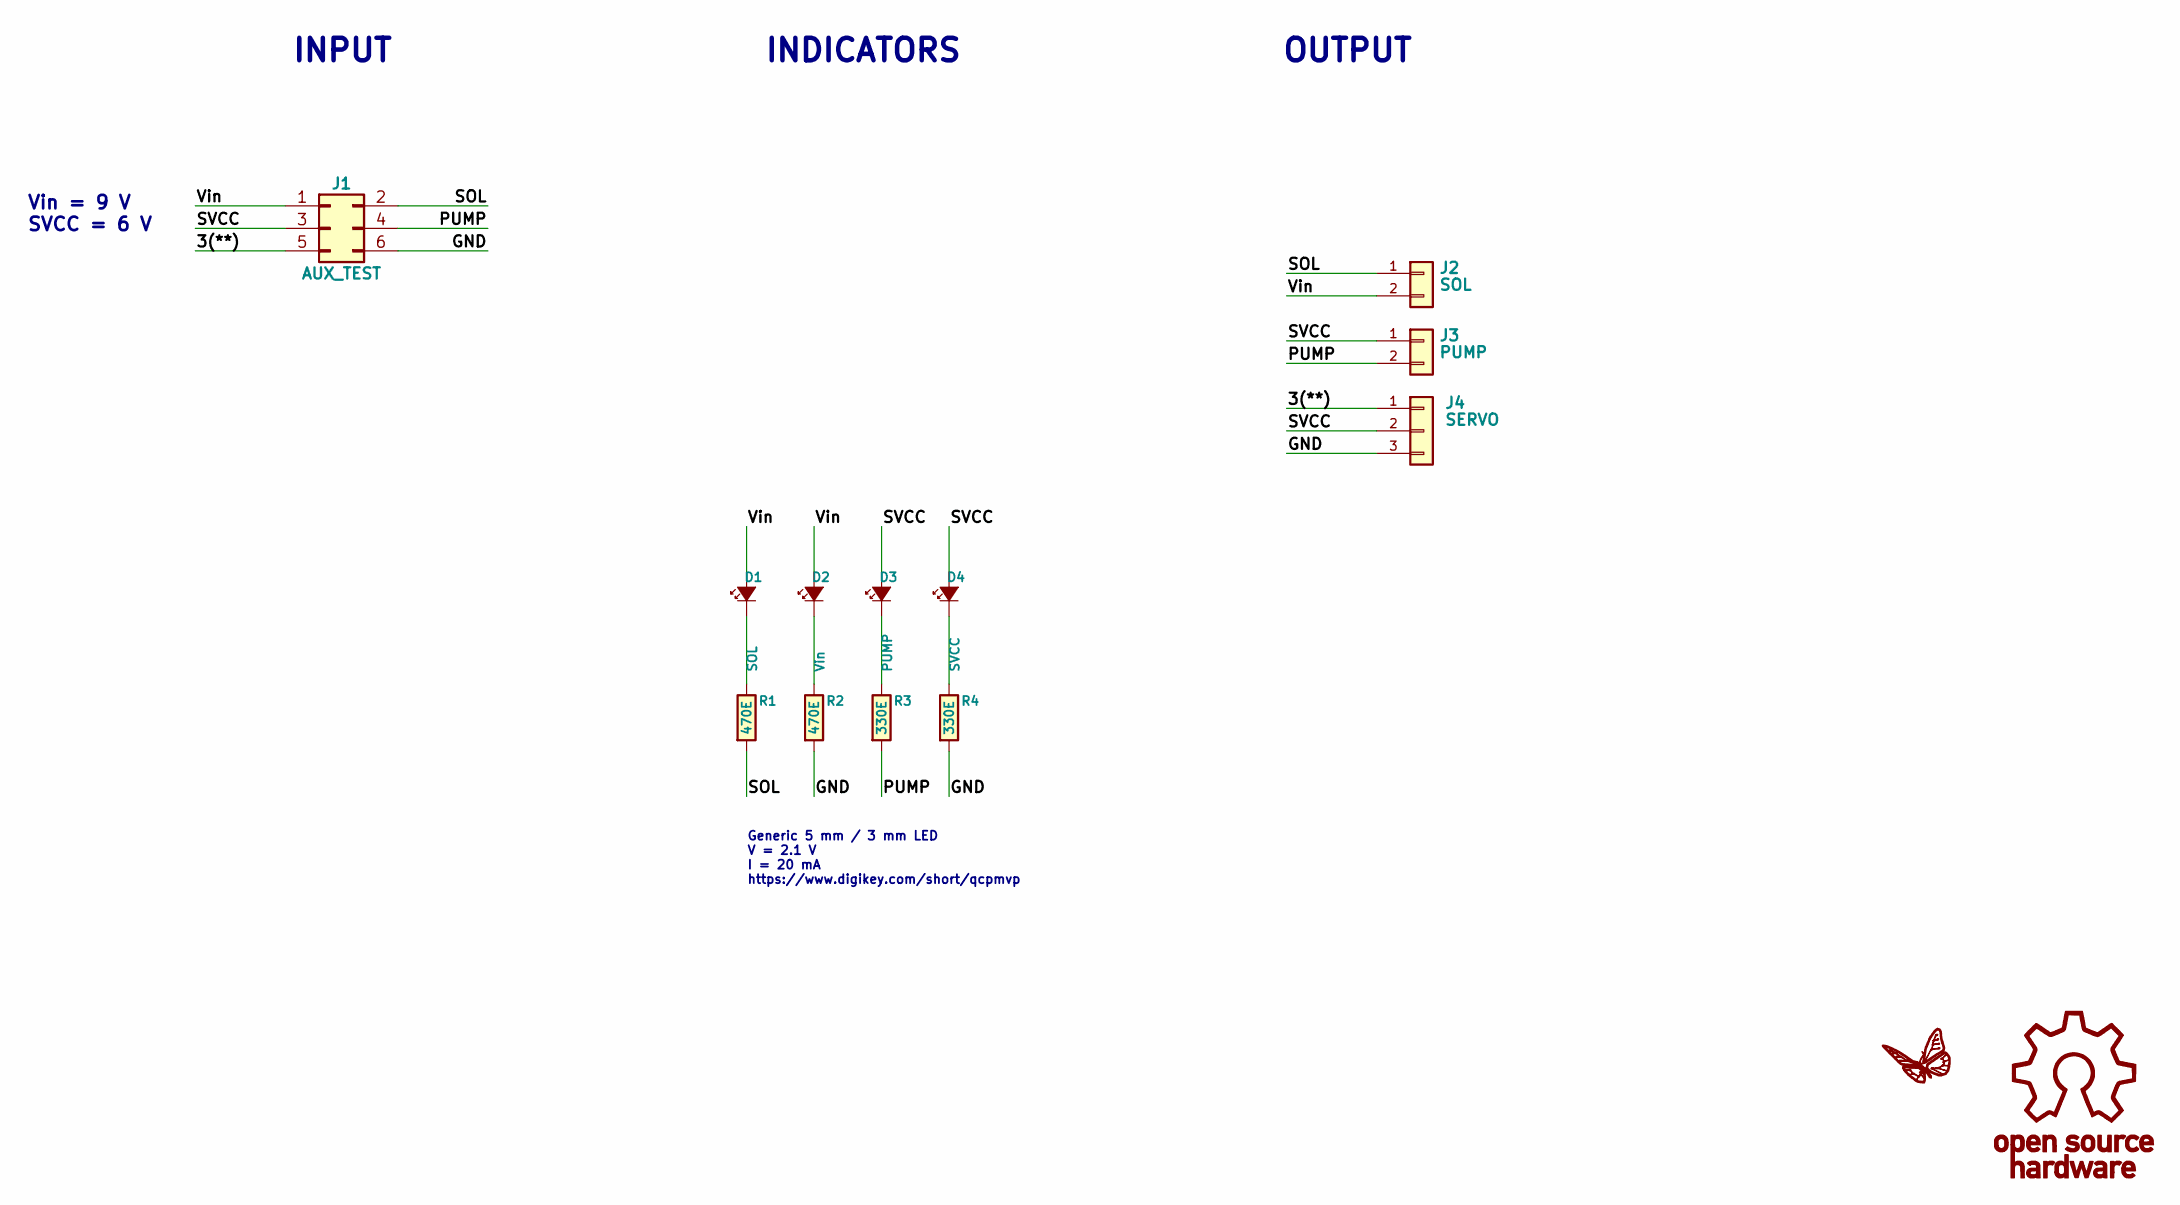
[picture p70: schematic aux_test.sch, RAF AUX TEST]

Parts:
D1: SOL; LED-5MM
D2: Vin; LED-5MM
D3: PUMP; LED-5MM
D4: SVCC; LED-5MM
J1: AUX_TEST; Pin_Header_Straight_2x03
J2: SOL; TerminalBlock_Pheonix_PT-5.0mm_2pol
J3: PUMP; TerminalBlock_Pheonix_PT-5.0mm_2pol
J4: SERVO; Pin_Header_Straight_1x03_Pitch2.54mm
R1, R2: 470E; Resistor_Horizontal_RM10mm
R3, R4: 330E; Resistor_Horizontal_RM10mm

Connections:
/3(**): J1.5, J4.1
/GND: J1.6, J4.3, R2.2, R4.2
/PUMP: J1.4, J3.2, R3.2
/SOL: J1.2, J2.1, R1.2
/SVCC: D3.1 (A), D4.1 (A), J1.3, J3.1, J4.2
/Vin: D1.1 (A), D2.1 (A), J1.1, J2.2
unnamed: D1.2 (K), R1.1
unnamed: D2.2 (K), R2.1
unnamed: D3.2 (K), R3.1
unnamed: D4.2 (K), R4.1

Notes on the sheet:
Generic 5 mm / 3 mm LED V = 2.1 V I = 20 mA https://www.digikey.com/short/qcpmvp
INPUT
INDICATORS
OUTPUT
Vin = 9 V SVCC = 6 V

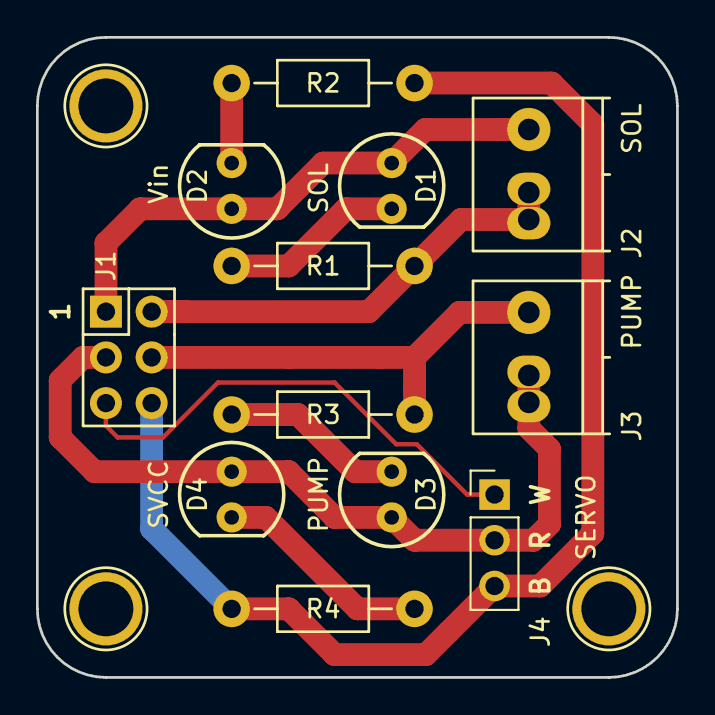
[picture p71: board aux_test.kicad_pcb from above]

Board: 2 copper layers, 35.6 x 35.6 mm, 15 parts (0 on the bottom side), 10 nets.

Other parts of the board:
1pin, 1pin#2, 1pin#3: VAL**; hole_3mm

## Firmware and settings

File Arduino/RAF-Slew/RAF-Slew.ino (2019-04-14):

//  Joystick moves the altitude / azimuth servos, but does not define
//  an absolute position.  This makes it easy to pick/refine
//  an aiming point.
//
//  The pump and solenoid timings are the same as in RAF2, but
//  you might want to adjust them as appropriate for the size
//  of your pump/reservoir/launchtube.

//  Change the next few #define's to suit your needs
#define AZIMUTH_HOME  90
#define AZIMUTH_DIRECTION 1 // Make -1 if you need to reverse azimuth movements
#define ALTITUDE_HOME  0
#define ALTITUDE_DIRECTION -1 // Make 1 if you need to reverse altitude movements
#define SOLENOID_FIRE_DURATION_MILLIS 300
#define PUMP_RECHARGE_MILLIS 3000
#define PUMP_INITIAL_CHARGE_MILLIS 10000
#define NULL_ZONE 50
#define JOY_MID 512

#include <Servo.h>

#define SOLENOID 2
#define PUMP 9
#define BUTTON 12
#define JOYX A0
#define JOYY A1
#define SERV1 3
#define SERV2 5

Servo azimuth;
Servo altitude;

void setup() {
  Serial.begin(115200);
  Serial.println("Ready Aim Fire!");

  //  Setup our fire button so it is off by default
  pinMode(BUTTON, INPUT_PULLUP);

  //  Setup the altitude/azimuth servos
  azimuth.attach(SERV1);
  azimuth.write(AZIMUTH_HOME);
  altitude.attach(SERV2);
  altitude.write(ALTITUDE_HOME);

  //  Setup the solenoid
  pinMode(SOLENOID, OUTPUT);
  digitalWrite(SOLENOID, LOW);

  //  Setup the pump, and run it for 10 seconds to prime reservoir
  pinMode(PUMP, OUTPUT);
  digitalWrite(PUMP, HIGH);
  delay(PUMP_INITIAL_CHARGE_MILLIS);
  digitalWrite(PUMP, LOW);
}

/*
   Utility function for updating a servo to a new value.
   This will be called twice (once for altitude, once for azimuth).

   Avoids jitter by allowing a "dead zone" near the joystick center.
   You can change the width of the dead zone with the NULL_ZONE #define
*/
int update_servo(int value, int pin, Servo servo, int high, int inversion) {
  int delta = analogRead(pin) - JOY_MID;
  if (abs(delta) > NULL_ZONE) {
    Serial.print("Incoming value is:  ");
    Serial.println(value);
    Serial.print("Current raw delta is:  ");
    Serial.println(delta);
    //  Upper bound of (map) is never hit, so we need to do -N, N+1 below...
    delta = map(delta, -JOY_MID, JOY_MID, -3, 4);
    delta *= inversion;
    Serial.print("Current mapped delta is:  ");
    Serial.println(delta);
    value = constrain(value + delta, 0, high);
    Serial.print("New value is:  ");
    Serial.println(value);
    servo.write(value);
  }
  return value;
}

/*
   Detects a request for launch, then
   fires the solenoid and recharges the air
   reservoir as required.
*/
void check_for_launch() {
  if (digitalRead(BUTTON) != LOW) {
    return;
  }

  Serial.println("fire!");

  //  Trigger solenoid, wait, then clear solenoid
  digitalWrite(SOLENOID, HIGH);
  delay(SOLENOID_FIRE_DURATION_MILLIS);
  digitalWrite(SOLENOID, LOW);

  //  Recharge the pump as required
  digitalWrite(PUMP, HIGH);
  delay(PUMP_RECHARGE_MILLIS);
  digitalWrite(PUMP, LOW);
}

/*
   Our main loop.  Not much to this one.
   Simply check for a launch, set the servo positions,
   delay for 1/50th of a second, and repeat.
*/
int current_azimuth = AZIMUTH_HOME;
int current_altitude = ALTITUDE_HOME;
void loop() {
  check_for_launch();
  current_azimuth = update_servo(current_azimuth, JOYX, azimuth, 180, AZIMUTH_DIRECTION);
  current_altitude = update_servo(current_altitude, JOYY, altitude, 90, ALTITUDE_DIRECTION);
  delay(20);
}

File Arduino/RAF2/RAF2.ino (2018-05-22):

#include <FastLED.h>

#include <Servo.h>

#define SOLENOID 2
#define PUMP 9
#define BUTTON 12
#define JOYX A0
#define JOYY A1
#define SERV1 3
#define SERV2 5
#define SERV3 6
#define LIGHT A2
#define TEMP A3
#define NEOPIXELPIN 8
#define NUM_LEDS 1
CRGB leds[NUM_LEDS];
#define DATA_PIN NEOPIXELPIN
#define BRIGHTNESS 20
Servo azimuth;
Servo elevation;
void setup() {
  FastLED.addLeds<WS2811, DATA_PIN, RGB>(leds, NUM_LEDS);
  FastLED.setBrightness(BRIGHTNESS);

  Serial.begin(115200);
  Serial.println("Ready Aim Fire!");
  

  azimuth.attach(SERV1);
  elevation.attach(SERV2);
  azimuth.write(80);
  elevation.write(3);
  pinMode(SOLENOID,OUTPUT);
  digitalWrite(SOLENOID,LOW);
  pinMode(PUMP,OUTPUT);
  digitalWrite(PUMP,HIGH);
  delay(10000);
  digitalWrite(PUMP, LOW);
  pinMode(BUTTON,INPUT_PULLUP);
  leds[0] = CRGB::Red;
  FastLED.show();
  delay(200);
  leds[0] = CRGB::Green;
  FastLED.show();
  delay(200);
  leds[0] = CRGB::Blue;
  FastLED.show();
  delay(200);
  leds[0] = CRGB::Black;
  FastLED.show();
 
}
void chase()
{
     // Move a single white led 
   for(int whiteLed = 0; whiteLed < NUM_LEDS; whiteLed = whiteLed + 1) {
      // Turn our current led on to white, then show the leds
      leds[whiteLed] = CRGB::White;

      // Show the leds (only one of which is set to white, from above)
      FastLED.show();

      // Wait a little bit
      delay(250);

      // Turn our current led back to black for the next loop around
      leds[whiteLed] = CRGB::Black;
      FastLED.show();
   }
}
int lastx;
int lasty;

void loop() {

  
 
  int light = analogRead(LIGHT);
  int temp = analogRead(TEMP);
  //Serial.print("LIGHT: ");Serial.print(light);Serial.print(" TEMP: ");Serial.println(temp);
   if (digitalRead(BUTTON) == LOW)
  {
    Serial.println("fire!");
    digitalWrite(SOLENOID,HIGH);
    delay(250);
    digitalWrite(SOLENOID,LOW);
    chase();
    digitalWrite(PUMP,HIGH);
    delay(3000);
    digitalWrite(PUMP, LOW);
    delay(100);
  }
 int xReading,yReading;
  xReading = analogRead(JOYX);
  yReading = analogRead(JOYY);

if(abs(lastx-xReading) > 2)
{
  if (xReading <490)
  {
    azimuth.write(map(xReading,490,0,90,2));
  }else
  if (xReading > 489)
  {
    azimuth.write(map(xReading,489,1023,91,178));
  }
  lastx = xReading;

}
if (abs(lasty-yReading) > 2)
{
  if (yReading <515)
  {
    elevation.write(map(yReading,515,0,31,70));
  }else
  if (yReading > 514)
  {
    elevation.write(map(yReading,524,1023,30,3));
  }
  lasty = yReading;
}

}

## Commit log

2017-05-15 Add arduino code
2017-05-15 add documentation
    [RAFbom.xlsx]
2017-05-16 add serial version, adjust servo senters for new pantilt
2017-05-17 fix fire func in rafserial, limits
    [RAFSerial.ino]
2017-05-19 add mounting plate
2017-05-22 add legs, move holes around a bit
    [leg.scad, leg.stl]
2017-07-13 update servo positions
2017-07-13 servo align sketch for pan tilt assembly
2017-07-24 initial commit, kicad version Ready Aim Fire Shield V2
    [RAF.kicad_pcb, RAF.sch]
2017-07-25 mostly finished schematic
2017-07-25 add sot23-6 footprint, fix drc errors
    [RAF.sch]
2017-07-25 add i2c header
    [RAF.sch]
2017-07-25 update footprint allocation
    [RAF.sch]
2017-08-01 new parts, initial layout, backup of switcher design
    [RAF-with-switcher.sch, RAF.kicad_pcb]
2017-08-02 layout and gerbers
    [RAF-B.Cu.gbl, RAF-B.Mask.gbs, RAF-B.Paste.gbp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]
2017-08-09 add pin 1 indications for LED and mosfet
    [RAF.kicad_pcb]
2017-08-22 add seeed bom
    [RAF_BoM_seeed.xls]
2017-08-23 updated do not populate
    [RAF_BoM_seeed.xls]
2017-08-23 add labels for the mosfet terminals
    [RAF.kicad_pcb]
2017-08-24 HW ver2 of kicad
    [RAF-B.Cu.gbl, RAF-B.Mask.gbs, RAF-B.Paste.gbp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]
2017-08-24 RAF v3 Kicad WIP
    [CP_Elec_4x5_7.step, DO-214AC_SMA.step, DPAK_TO-252AA.step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]
2017-08-25 add pcb spec file for Seeed
    [03-RAF_PCB_specification.xlsx]
2017-08-25 RAF v2.1 kicad layout
    [CP_Elec_4x5_7.step, DO-214AC_SMA.step, DPAK_TO-252AA.step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]
2017-08-25 folder rename
    [03-RAF_PCB_specification.xlsx]
2017-08-25 update bom for cds and datasheet
    [RAF_BoM_seeed.xls]
2017-08-25 LDR footprint modified
    [RAF-B.Cu.gbl, RAF-B.Mask.gbs, RAF-B.Paste.gbp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]
2017-08-25 removed kicad_v2 folder
2017-08-26 PCB ver2.1 complete, added variable resistor for LDR
    [RAF-B.Cu.gbl, RAF-B.Mask.gbs, RAF-B.Paste.gbp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]
2017-08-26 kicad_v2.1 updated silkscreen
    [03-RAF_PCB_specification.xlsx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]
2017-08-26 added FreeCad and step models of PCB to fabricate folder
    [RAF.kicad_pcb, Resistor_LDR_5_0x3_4.step]
2017-09-05 seeed joystick revision
    [RAF (copy).sch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]
2017-09-05 joystick 3D updated
    [ALPS_JOYSTICK.step, RAF (copy).sch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]
2017-09-05 updated 3D model in fabricate
    [RAF.FCStd]
2017-09-06 added pogo connector for testing solenoid, pump, servo
    [RAF.kicad_pcb, RAF.sch]
2017-09-06 cleaned up silk legend
    [RAF-B.Cu.gbl, RAF-B.Mask.gbs, RAF-B.Paste.gbp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]
2017-09-07 aux_text board for production testing
    [RAF.FCStd, aux_test.kicad_pcb, aux_test.sch]
2017-09-08 aux_test minor mods
    [aux_test-B.Cu.gbl, aux_test-B.Mask.gbs, aux_test-B.SilkS.gbo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]
2017-09-18 fix C2 and C7 value, update to 5mm screw terminals
    [RAF_BoM_seeed.xls]
2017-09-20 pin 1 markers added on silk legend
    [RAF-B.Cu.gbl, RAF-B.Mask.gbs, RAF-B.Paste.gbp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]
2017-09-21 fix servo legend
    [aux_test.kicad_pcb]
2017-09-21 fixed errors in aux_test layout
    [Header_Male_03Pin.step, LED_5mm.step, Res40-Axial_Short_0.25W-10R.step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]
2017-09-22 updated aux_test PCB
    [Header_Male_03Pin.step, LED_5mm.step, RAF.kicad_pcb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]
2017-09-22 added aux_test gerber
2017-10-02 update bom with links
    [RAFbom.xlsx]
2017-10-03 modified screw terminal solder pads
    [RAF-B.Cu.gbl, RAF-B.Mask.gbs, RAF-B.Paste.gbp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]
2017-10-06 remove tactile switch
    [RAF_BoM_seeed.xls]
2017-10-09 edited values of C2,C7
    [RAF.kicad_pcb, RAF.sch, RAF_BoM_pcb.csv.ods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]
2017-12-20 add missing 3d printed pieces
    [BarrelHolder_mm_flatBack.stl, solenoid_holder.stl]
2017-12-22 add assembly v2 images
    [BarrelHolder v9.stl, BarrelHolder_mm_flatBack.stl]
2017-12-22 update for v2 and air pump
    [RAFbom.xlsx]
2018-01-02 New V2 assembly instructions (incomplete)
2018-01-02 finished through Pneumatic assembly.
2018-01-02 incremental update to assembly instructions
2018-01-02 Link in assembly instrcutions
2018-01-02 and done with Assembly.md
2018-01-03 add formatted assembly instructions
2018-01-09 update bom
    [RAFbom.xlsx]
2018-05-22 update raf2 for new servos
2018-06-06 add barrelholder, update solenoid holder
    [BarrelHolder.stl]
2018-07-27 add airmount pcb
    [airmount-B.Cu.gbl, airmount-B.Mask.gbs, airmount-B.Paste.gbp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]
2018-07-28 Airmount _v2 and _v3
    [03-RAF_PCB_specification.xlsx, ALPS_JOYSTICK.step, CP_Elec_4x5_7.step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]
2018-07-28 Airmount _v2 and _v3 revised gerbers
    [airmount-B.Cu.gbl, airmount-B.Mask.gbs, airmount-B.SilkS.gbo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]
2020-01-08 Add instructor materials, move tools into section
2020-01-10 add new assembly photos
2020-01-10 Start inserting new pictures
2020-01-10 mv v3 assembly images
2020-01-10 interim assembly edits
2020-01-27 change picture, remove obsolete bom
